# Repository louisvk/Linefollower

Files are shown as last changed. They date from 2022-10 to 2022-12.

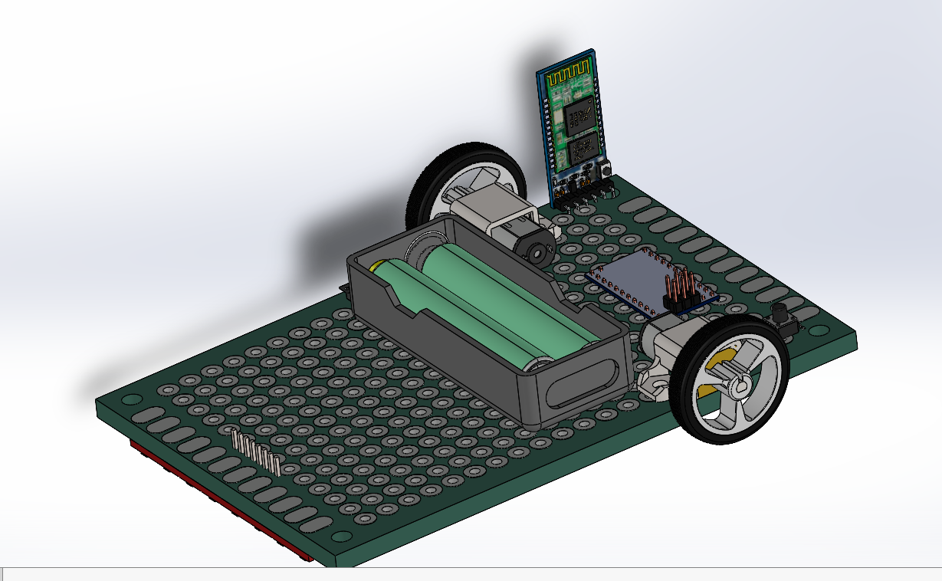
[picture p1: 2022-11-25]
technische tekeningen/mechanisch/MicrosoftTeams-image.png

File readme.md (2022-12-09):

316579205_587818479776314_3724272411660619265_n

# LineFollower
<br />
lege repository die je als template kan gebruiken om een eigen repository te starten voor uw linefollower project
<br />
<br />
[picture]
<br />
<br />
  
## specifications
<br />
microcontroller: Pololu baby orang-oetan B-328
<br />
motors: 30:1 Micro Metal Gearmotor LP 6V
<br />
h-bridge: TB752A16612FNG (zit op de microcontroller)
<br />
sensors: QTR-8A Reflectance Sensor Array
<br />
batteries: 2x18650
<br />
wireless communication: HC-05
<br />
distance sensor - motors: 10cm
<br />
weight: 200g
<br />
speed: 0.601m/s
<br />

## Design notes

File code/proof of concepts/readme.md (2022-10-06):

# Proof of Concepts

Een proof of concept is een combinatie van minimale hard- en software om eenvoudig aan te tonen dat iets werkt.  
Proof of concepts kunnen enerzijds als eerste poging dienen om een bepaald onderdeel van het project werkend te krijgen. Anderzijds kunnen ze tijdens het debuggen van het finale project dienen als test om eventuele hardware problemen te elimineren bij onduidelijke problemen.
<br />  
<br />
Een proof of concept bestaat uit
* een elektronisch schema (indien van toepassing)
* minimale code om de voorop gestelde zaken te demonstreren
* minimale uitleg / aandachtspunten
<br />
De elektronische schakelingen van de proof of concepts komen bij voorkeur overeen met deze van de uiteindelijke linefollower, zodat de code zonder aanpassingen op het finale project kan draaien.

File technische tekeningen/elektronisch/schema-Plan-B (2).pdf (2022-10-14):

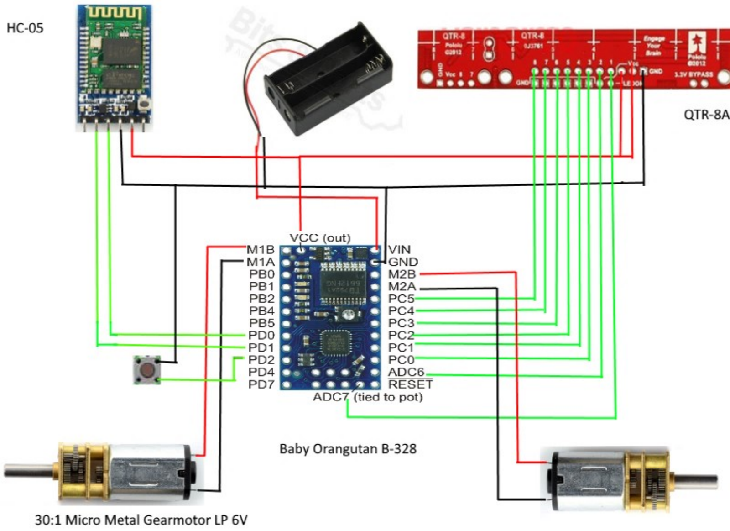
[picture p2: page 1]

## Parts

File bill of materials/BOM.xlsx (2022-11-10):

Volgnummer | Naam | Omschrijving | Nieuw/Recup | Kostprijs/Stuk | Aantal | Subtotaal
1 | 30:1 Micro Metal Gearmotor LP 6V | Motoren | Nieuw | 12.15 | 2 | 24.3
2 | QTR-8A Reflectance Sensor Array | Sensoren | Nieuw | 11.35 | 1 | 11.35
3 | 18650 | Batterijen | Nieuw | 3.92 | 2 | 7.84
4 | 2x18650LEADSHOL | Batterijhouder | Nieuw | 1.5 | 1 | 1.5
5 | HC05 | Bluetoothmodule | Nieuw | 6.96 | 1 | 6.96
6 | MOT-MICKROM-BRACKET | Motorhouders | Nieuw | 5.06 | 1 | 5.06
7 | Pololu Wheel 40x7 | Wielen | Nieuw | 2.45 | 2 | 4.9
8 | Printplaat | Printplaat | Nieuw | 3.558 | 1 | 3.558
9 | Pololu baby orang-oetan B-328 | Microcontroller + H-brug | Nieuw | 16.8 | 1 | 16.8
10 | AVR programmer V2 | Programmer | Nieuw | 3.74 | 1 | 3.74
11 | M3x35 platte kop | Bout | Nieuw | 0.1 | 1 | 0.1
12 | Oplader 18650 | Oplader batterijen | Nieuw | 14.99 | 1 | 14.99
13 | 1825910-6 | Drukknop | Recup | 0 | 1 | 0
14 | Bobeini SPDT 1P2T | Schuifschakelaar | Nieuw | 0.78 | 1 | 0.78
 |  |  |  | Totaal | = | 101.878

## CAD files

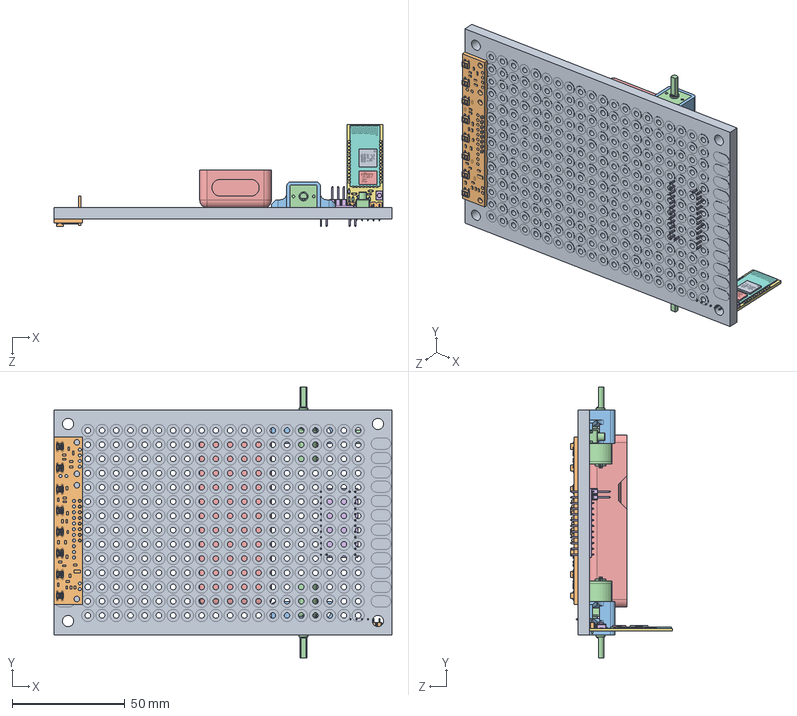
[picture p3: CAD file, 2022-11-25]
technische tekeningen/mechanisch/Mechanisch ontwerp.SLDASM
150.0 x 120.2 x 45.4 mm
pcb_proto_board(40x60)
Qtr-8A
bracket micro metal gearmotor x 2
Micro Metal Gear Motor x 2
2xAAA
orangutan baby
HC-05 part1
HC-05 part3
HC-05 part2
HC-05 part5
HC-05 part6 x 6
HC-05 part7 x 6
HC-05 part4
tactileswitch-short
HC-05 part8 x 4
HC-05 part9 x 4
HC-05 part10
HC-05 part11 x 18
HC-05 part12
push_button.stp
Sliding Switch.step

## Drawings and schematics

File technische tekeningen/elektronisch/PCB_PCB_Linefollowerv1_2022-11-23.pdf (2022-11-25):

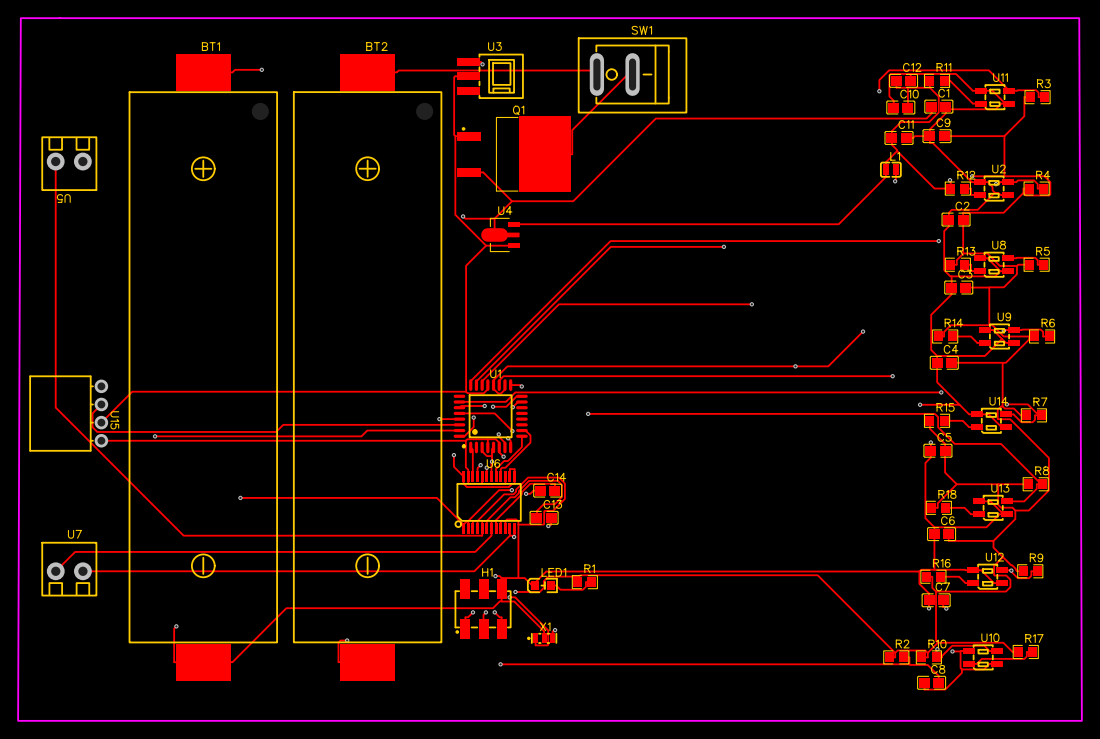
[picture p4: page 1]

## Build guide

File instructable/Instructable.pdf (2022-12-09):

# INSTRUCTABLE LINEFOLLOWER

### Abstract

Een beknopt stappenplan om zelf een linefollower te maken. Met verduidelijkingen om niet dezelfde problemen te moeten oplossen als ons.

Instructable linefollower

1

## Inhoud

2

## 1. Componenten en benodigdheden

Aller belangrijkst voor het voltooien van dit project is het bemachtigen van alle benodigde componenten. Deze componenten staan allemaal opgelijst in de BOM. Bij elk component staat ook de prijs waarvoor wij deze aangekocht hebben. Zo heb je een idee van de kostprijs voor je aan het project begint.
Naast de componenten is het juiste gereedschap ook van groot belang voor het voltooien van dit project.:
- Computer
- AVR programmer V2
- Android smartphone
- Soldeerbout
- Boormachine
- Slijpschijf
- Kniptang
- Striptang
- Kleine boren
- Stift voor aftekenen
- Lat
- Breekmesje

## 2. Printplaat

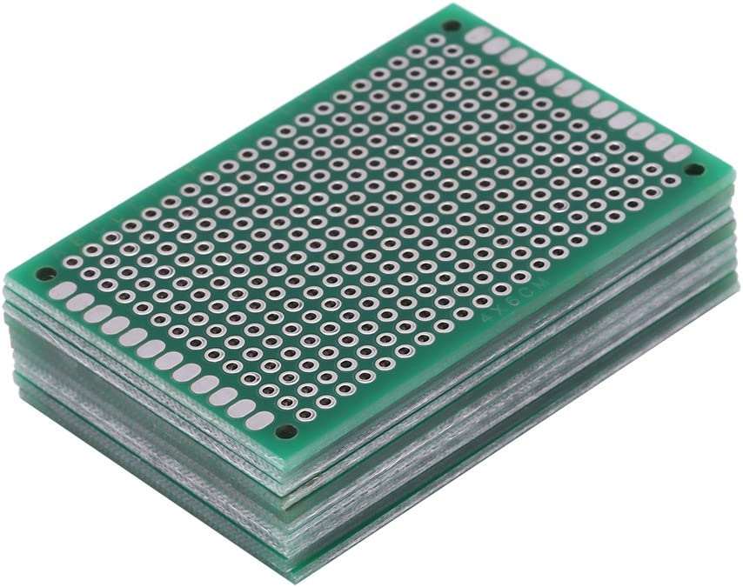
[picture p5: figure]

Figuur 1: printplaten
1. Zorg dat de printplaat eerst op maat is volgens de mechanische tekening. Je kan dit doen door eerst de afmetingen op de printplaat te zetten en vervolgens met een breekmesje langs een lat een groef te snijden. Wanneer je dit doet kan je eenvoudig de printplaat afbreken.

### 2. Nadat de printplaat op maat is gebracht kunnen de gaten worden geboord voor het

monteren van de motoren. Ook deze afmetingen zijn terug te vinden op de mechanische tekening.

3

3. Nu er toch geboord wordt kan je zo goed ook het gat boren voor de moer voorop de kar.

### 4. Er kan eventueel nog eens met schuurpapier of een slijpschijf langs de randen gegaan

worden om deze mooi effen en glad te maken.

### 5. Nu mogen ook de motoren, sensor, batterijhouder en Orangutan op de printplaat

gemonteerd worden. Enkel voor de motoren en batterijhouder moet er met moeren en bouten gewerkt worden. De sensor en Orangutan zullen vanzelf vast komen wanneer deze gesoldeerd worden.

### 6. Nu kunnen ook de wielen op de motoren gemonteerd worden. Dit kan door ze er gewoon

over te schuiven.

## 3. Solderen

### 3.1. Motoren:

- Hiervoor strip je van 4 geleiders beide kanten 3mm af en vertin je deze.
- Eenmaal vertind kunnen deze van de motoren naar de juiste pinnen op de Orangutan gebracht worden (volgens het elektronisch schema).
- Er kunnen eventueel ook krimpkousen over de solderingen aangebracht worden. Dit zorgt voor een beter, mooiere afwerking.

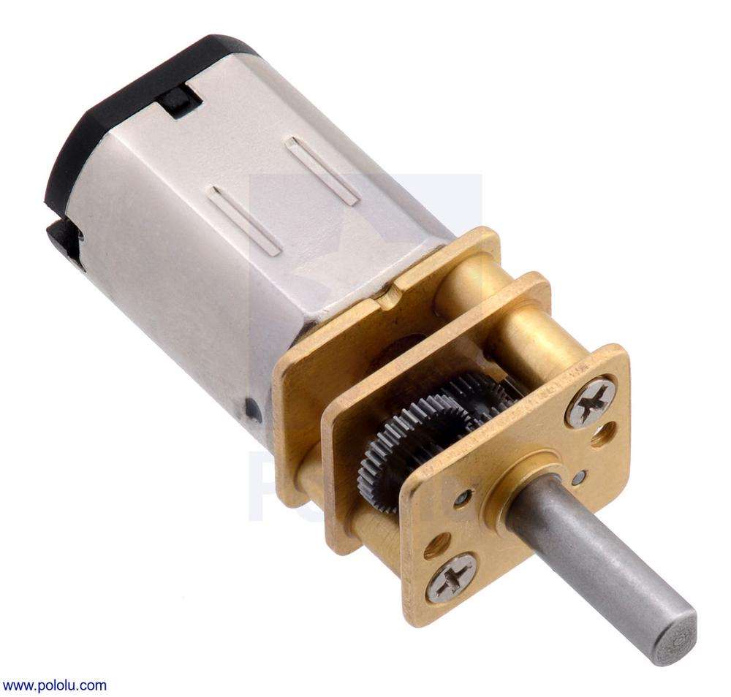
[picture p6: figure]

Figuur 2: DC motor 30:1

### 3.2. Batterijhouder:

- De ground van de batterijhouder mag rechtstreeks verbonden worden met de ground van de Orangutan.
- De Vcc van de batterijhouder moet eerst aan de schuifschakelaar op de printplaat gesoldeerd worden. Vanaf deze schuifschakelaar mag de plus naar de Orangutan gebracht worden en ook vast gesoldeerd worden.

### 3.3. Sensor array:

- Voor de sensor array strippen we 10 kabels van 10 cm aan beide zijden 3 mm.
- We beginnen met de 2 voeding kabels aan de sensor array en de Orangutan te solderen.

4

- Nu kunnen we de aparte sensoren aansluiten aan de Orangutan. Dit is belangrijk dat dit een voor een gebeurt omdat we zo de kans op mis aansluiten verkleinen.
- Nu kunnen de kabeltjes eventueel onder de batterijhouder gebracht worden, dit zorgt voor een nettere afwerking.

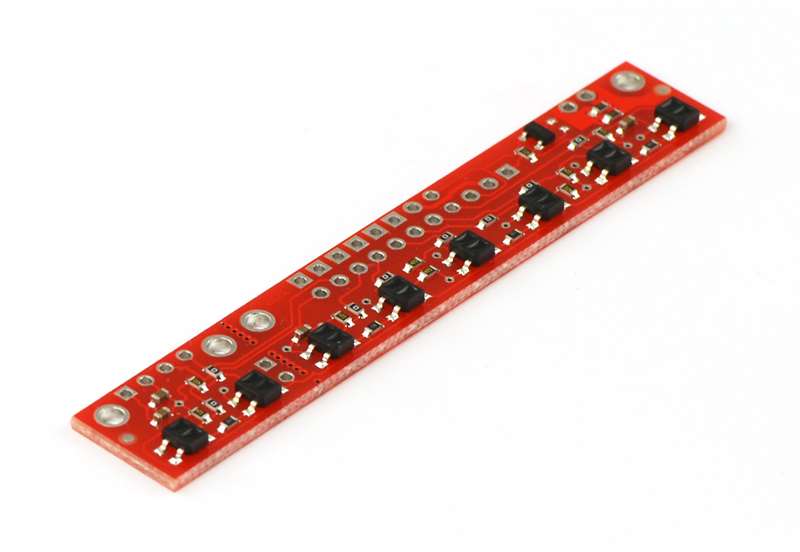
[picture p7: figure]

Figuur 3: QTR-8A

### 3.4. Drukknop

- Plaats de drukknop op de printplaat.
- Verbind de ene kant met de ground (er wordt een met een PULL UP gewerkt).
- De andere kant verbind je met de overeenkomende pin terug te vinden op het elektrisch schema.

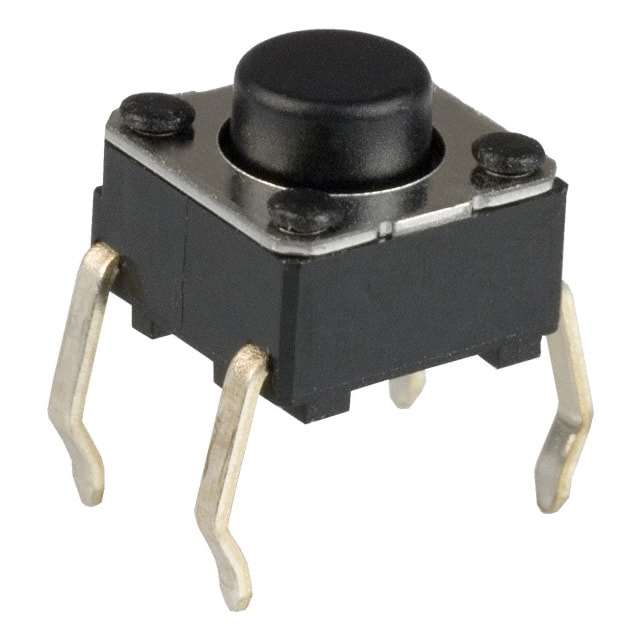
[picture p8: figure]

Figuur 4: Drukknop

## 4. Ingebruikname AVR programmer

### 4.1. Downloaden benodigde bestanden/programma’s

Bestanden:
o Hardware map | => te vinden op de Pololu site
o AVR programmer applicatie | => te vinden op de Pololu site

5

### 4.2. Installeren bestanden/programma’s

### 4.2.1. De hardware map

Deze moet geplaatst worden in de Arduino map te vinden in je documenten. Dit is nodig om het juiste board aan te kunnen duiden.
Pad: C:\Users\Louis\Documents\Arduino\hardware

### 4.2.2. AVR programmer

Eenmaal gedownload het execute programma openen en de stappen doorlopen. Normaal gezien zou je nu in de arduino applicatie bij programmers de AVR programmer moeten kunnen aanduiden.
Is dit niet het geval?
- Ga naar apparaat beheer druk op USB apparaten en doe rechterklik update. Nu zou hij wel zichtbaar moeten zijn.

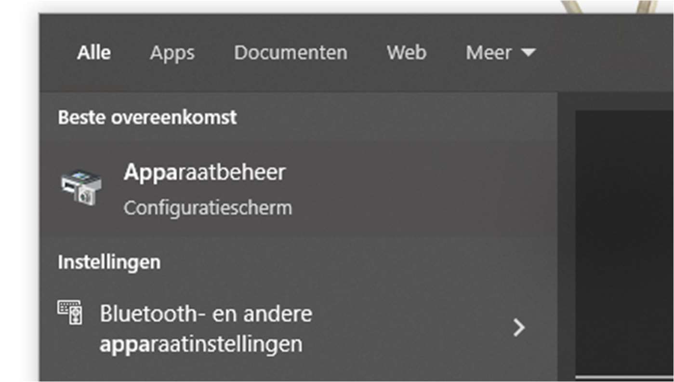
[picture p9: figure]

Figuur 5: Apparaatbeheer

## 5. App

Hiervoor is een Android smartphone nodig. We downloaden de app: Serial Bluetooth Terminal

## 6. Ingebruikname

1) Verbind de AVR programmer met jouw computer en de Orangutan. (zorg dat de spanning van de batterijen afligt.
2) Open /technisch dossier/Plan B – rijdt afgewerkt/code/finaal met de arduino IDE software
3) Klik op Hulpmiddelen > Board: > Pololu Orangutan
4) Klik op Hulpmiddelen > Programmer > AVR programmer

6

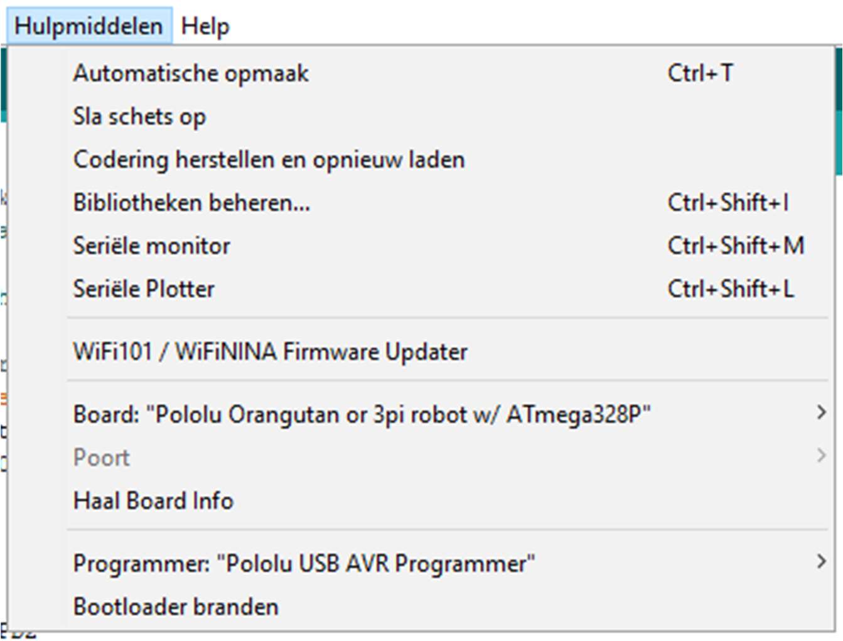
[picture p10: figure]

Figuur 6: Board + programmer
5) Upload het programma
6) Koppel de AVR programmer los
7) Stop 2 18650 batterijen in de batterijhouder
8) Als je nog niks ziet gebeuren verander de schuifschakelaar dan eens van positie
9) Start jouw bluetooth app op je smartphone op en verbind met de linefollower
10) Stel de volgende parameters in:
‘Set cycle 1500’
‘Set power 100’
‘Set diff 0.5’
‘Set kp 10’
‘Set ki 0’
‘Set kd 0’
11) Kalibreer de sensoren van de linefollower
– Hou de sensoren boven een zwart vlak en zend ‘Calibrate black’. De linefollower antwoord – Hou de sensoren boven een wit vlak en zend ‘Calibrate white’. De linefollower antwoord
12) Hou de linefollower in het midden boven een zwarte lijn en zorg dat de wielen zweven door iets onder de achterkant te stoppen
13) Zend ‘Start’ of druk op de pushbutton. De wielen zouden moeten beginnen draaien. Zend ‘Start’ of druk op de pushbutton om te stoppen

7

14) Indien de wielen niet beide vooruit draaien moet je in het programma de motorpinnen van des betreffende motor omdraaien.
15) Laat de motoren opnieuw draaien. Indien je de linefollower verplaatst zodat de zwarte lijn onder 1 van de uiterste sensoren komt te liggen, moet de motor aan de kant van de zwarte lijn achterruit draaien en de andere sneller vooruit dan daarnet.
16) Nu kan je beginnen met de linefollower af te regelen. Deze waarden zijn voor elke linefollower anders.

## Figuurlijst
